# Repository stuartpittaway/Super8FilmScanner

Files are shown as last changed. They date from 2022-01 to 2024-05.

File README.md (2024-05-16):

# 3D printed Super 8 Film Scanner

Using OpenCV and Open Source software to scan and create videos from Super 8 film reel, along with a 3D printed frame.

The code and scanner were created quickly to achieve the job of scanning a handful of Super 8 reels at an acceptable quality.

The code is not optimised or user friendly, but pull requests are very welcome!

The code is unlikely to run straight out of the box on your computer/system, it will need minor amendments to folder names/paths etc.

Items needed for this project:
* [Raspberry Pi 4](https://www.raspberrypi.com/products/raspberry-pi-4-model-b/)
* [Pi Advanced 12megapixel Camera](https://www.raspberrypi.com/products/raspberry-pi-high-quality-camera/)
* [Microscope lens for the Raspberry Pi High Quality Camera - 0.12-1.8x](https://shop.pimoroni.com/products/microscope-lens-0-12-1-8x)
* 3D printed frame (files in this repository)
* Two small depth stepper motors (NEMA 17 style)
* RAMPS style motherboard for controlling the stepper motors and running [MARLIN](https://github.com/MarlinFirmware/Marlin)
* Two stepper drivers (for example A4988)
* ~5000K "cool white" MR16 style LED light bulb (5 Watt)
* 240V Power supply (an old Ender3 PSU will do)
* MicroSD card

# YouTube video

See the video on how to use and build this device.

https://youtu.be/rd1Xu6e6nrw

# Setup

This is a rough setup description and some steps might be missing, but here is what's necessary:

## Step 1 - Flash Marlin to the mainboard
Flash your mainboard with the Marlin Firmware. You can find the latest release [here](https://marlinfw.org/meta/download/).

Open Arduino IDE, make the required changes (for your mainboard), connect the Mainboard via USB and upload the firmware to the Mainboard.

## Step 2 - Install RaspOS on the Raspberry Pi
Install the Raspberry Pi Imager, which you can find [here](https://www.raspberrypi.com/software/).

Plug in the microSD card into your computer and choose to install the **Legacy 32-bit OS** in the imager software. Use CTRL+SHIFT+X to open the advanced settings.  Choose a hostname, for example "scanner". Then add a username and password. Activate SSH under "services" and add your Wifi settings.

## Step 3 - Wiring
Assemble the scanner according to the 3D files.

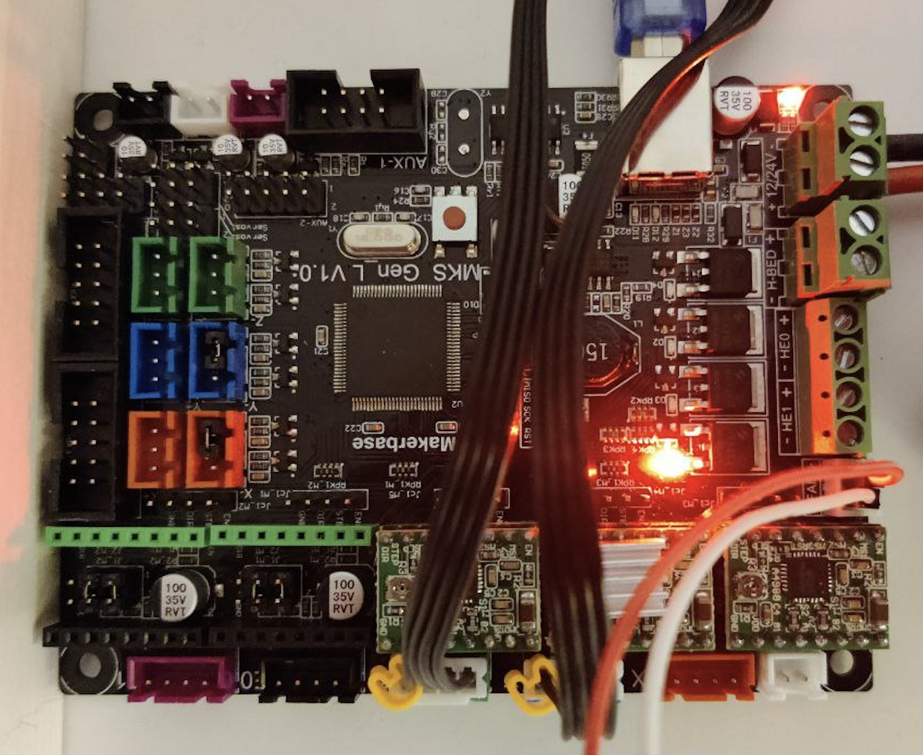
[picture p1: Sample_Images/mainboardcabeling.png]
Mainboard


Plug in the stepper drivers into the mainboards Y and Z axis, then plug in the stepper motors in these axis. You should add the heatsink to the Y axis stepper driver, as it's the one used the most.

Slot the Raspberry Pi HQ cameras ribbon cable into the Raspberry Pi and lock it in place. 

Plug the LED wires into the fan header. 

Connect the power supply to the mainboard via the two cables. Make sure the power supply is disconnected.

Connect the mainboard to the Raspberry Pi.

## Step 4 - Connecting to the Raspberry Pi
If you don't plan to use the scanner with dedicated monitor, keyboard and mouse, you have to connect to it via Terminal and VNC. 

Turn on the Raspberry Pi and the PSU. 

Use SSH to connect to <username>@scanner.local, then install VNC server to control your scanner in the future. If your screen stays black after connecting, run "vncserver-virtual" to add a virtual display. 

## Step 5 - Install dependencies
To install OpenCV, run `sudo apt-get update` , then `sudo apt-get install build-essential cmake pkg-config libjpeg-dev libtiff5-dev libjasper-dev libpng-dev libavcodec-dev libavformat-dev libswscale-dev libv4l-dev libxvidcore-dev libx264-dev libfontconfig1-dev libcairo2-dev libgdk-pixbuf2.0-dev libpango1.0-dev libgtk2.0-dev libgtk-3-dev libatlas-base-dev gfortran libhdf5-dev libhdf5-serial-dev libhdf5-103 python3-pyqt5 python3-dev -y`

you might also need to run `pip install opencv-python==4.5.3.56` .

# Scanning Process

## Step 1 - Capture full frame masters

On a Raspberry Pi (4 is possible), use the python code in `RasPi_Camera_Super8Scanner.py` to capture all the individual frames to individual PNG files.

This will generate a large number of files (3000+) of significant file size 2+MByte each.  Camera captures approximately 3megapixel images.

Scanning is slow, running around 1.25 frames per second, so a 3 minute reel takes 1 hour.  

Speed was not a critical issue when designing this solution, however the longest delay is capturing the image from the Raspberry Pi camera.

The images captured would look like this (only higher resolution).  Notice you can see the sproket hole and the black border on the right of the image.
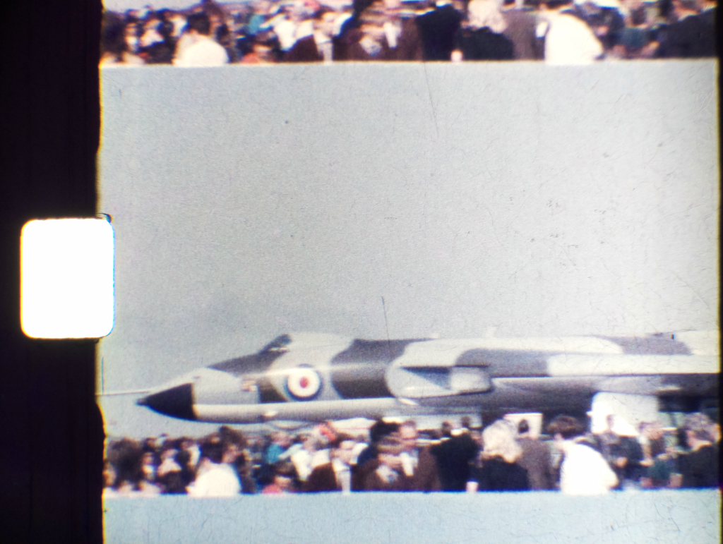
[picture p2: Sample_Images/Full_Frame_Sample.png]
Full frame sample image


## Step 2 - Alignment

Step one captured the full frame of the film, this process takes those master images and accurately crops them to vertically and horizontally align them based on the sproket hole.

OpenCV is used to detect the hole and align/crop the image.

The code is in `ImageRegistrationCropping.py` its likely you will need to tweak the code to cater for the particular file size/resolution you are using and the camera configuration.

Look for the variable `frame_dims` to control the output image dimensions.  Its likely you will also need to change the folder names.

The files are put into a folder named "Aligned".  Example image.
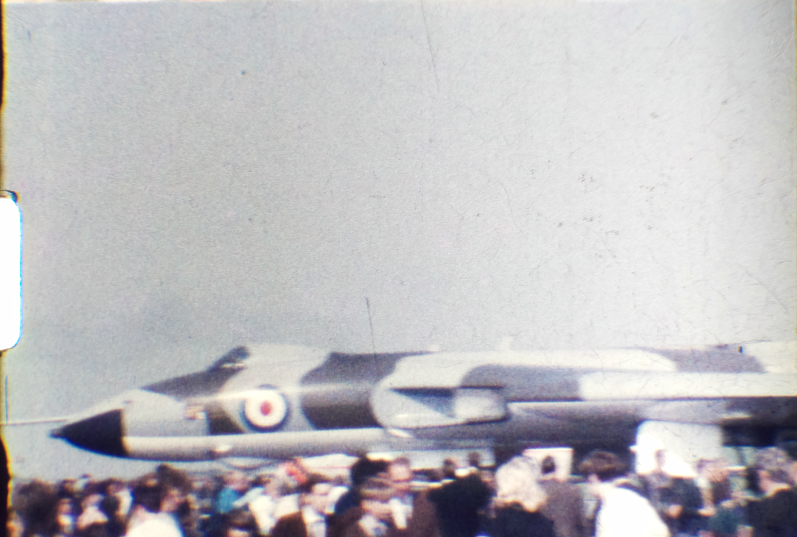
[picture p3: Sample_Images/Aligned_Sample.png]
Aligned frame sample image


You can modify the provided `config.json` file to suit your needs. These are the available configurations:

```json
{
    "image_name": "frame_????????", // The name of the images to be processed
    "input_path": "Capture", // The folder where the images are stored
    "output_path": "Aligned", // The folder where the aligned images will be stored
    "extensions": ["png", "jpg", "jpeg"], // The extensions of the images to be processed
    "average_sample_count": 11, // This will be saved automatically if you run a new analysis
    "average_width": 512, // This will be saved automatically if you run a new analysis
    "average_height": 649, // This will be saved automatically if you run a new analysis
    "average_area": 306419, // This will be saved automatically if you run a new analysis
    "resize_image": [ // if you want to resize the images after alignment
        3840, // width
        2160 // height
    ],
    "frame_dims": [ // You can get this after adjusting the first frame dimensions
        0, // x offset
        -904, // y offset
        3192, // width
        2305 // height
    ]
}
```

## Step 3 - Denoise (optional)

A post process called de-noise filtering can be used to improve image quality.  This code can be found in `Denoise.py`

This is a significantly slow process, so a faster CPU helps a lot.  You can tweak the amount of correction made with these values

```
h=3, hColor=3, templateWindowSize=7,searchWindowSize=29
```

For a description of the paramters, check out the [OpenCV documentation](https://docs.opencv.org/3.4/d1/d79/group__photo__denoise.html#gaa501e71f52fb2dc17ff8ca5e7d2d3619).

The files are put into a folder named "Denoise".  Example image.
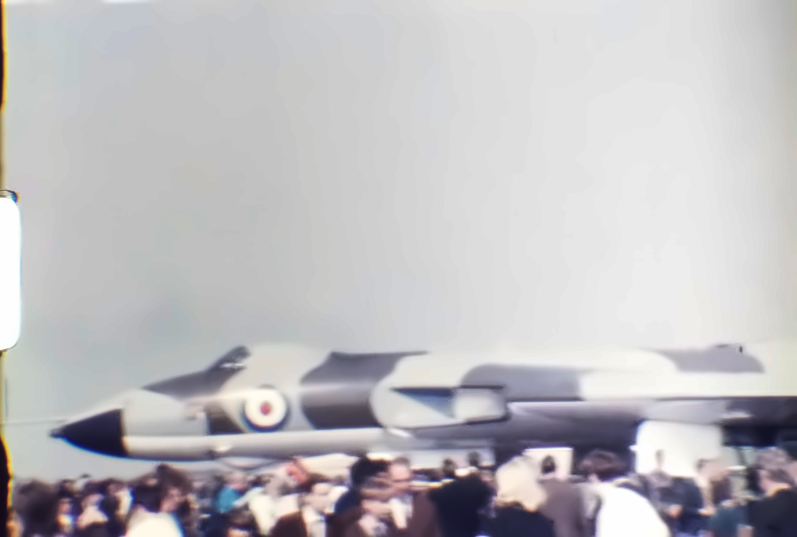
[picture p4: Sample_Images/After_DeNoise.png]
Frame after denoise filtering


## Step 4 - Create Video

### FFMPEG
You can use the open source FFMPEG tool to convert a series of pictures into a video, using a command similar to this:
```
ffmpeg.exe -y -start_number 0 -framerate 18 -i "Aligned\frame_%08d.png" -vcodec h264 -preset slower -tune grain -crf 15 -vf "fps=18,format=yuv420p" -r 18 film_output.mp4
```

### Video editor software
Alternatively, use video editing software like [Davinci Resolve](https://www.blackmagicdesign.com/products/davinciresolve/) to import the pictures and generate a video.

This can also be used to colour correct the film, remove noise and grain and generally improve the final video.

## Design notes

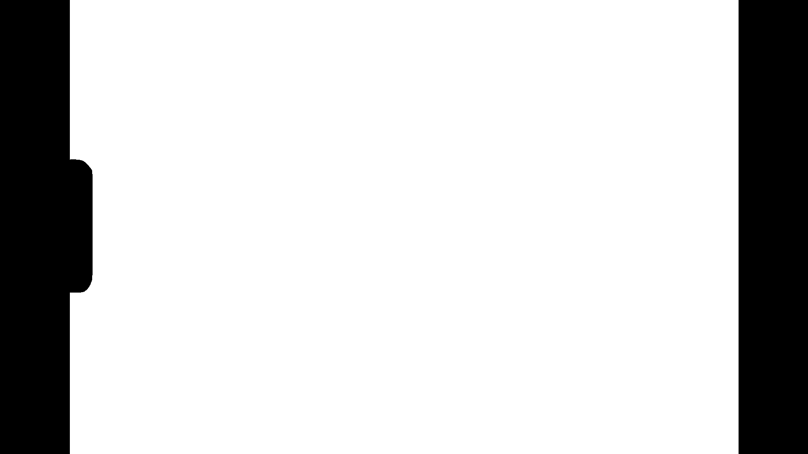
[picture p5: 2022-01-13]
Python/overlay_frame.png

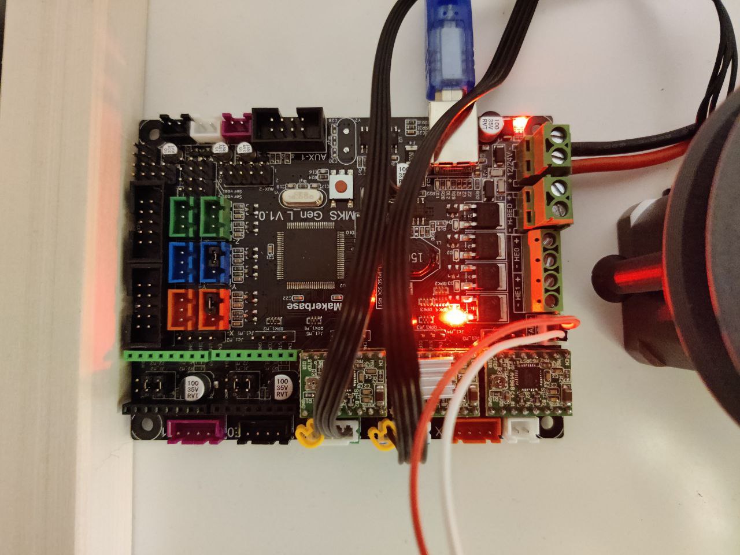
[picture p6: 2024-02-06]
Sample_Images/mainboard.jpg

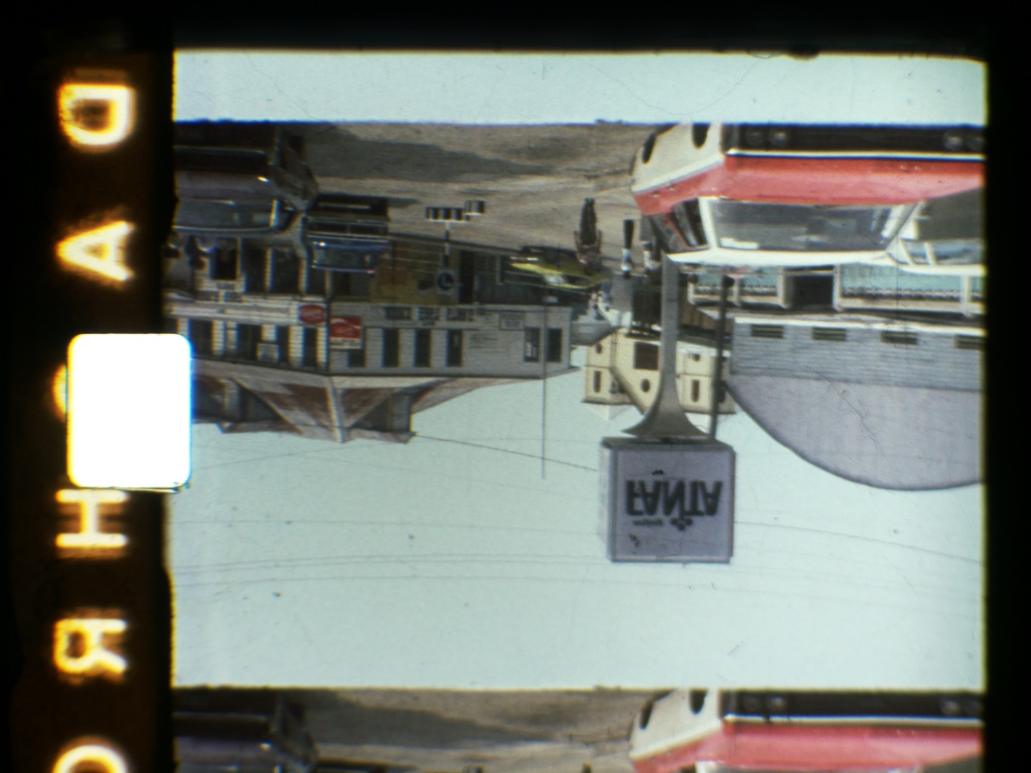
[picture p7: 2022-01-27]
Python/grab.jpg

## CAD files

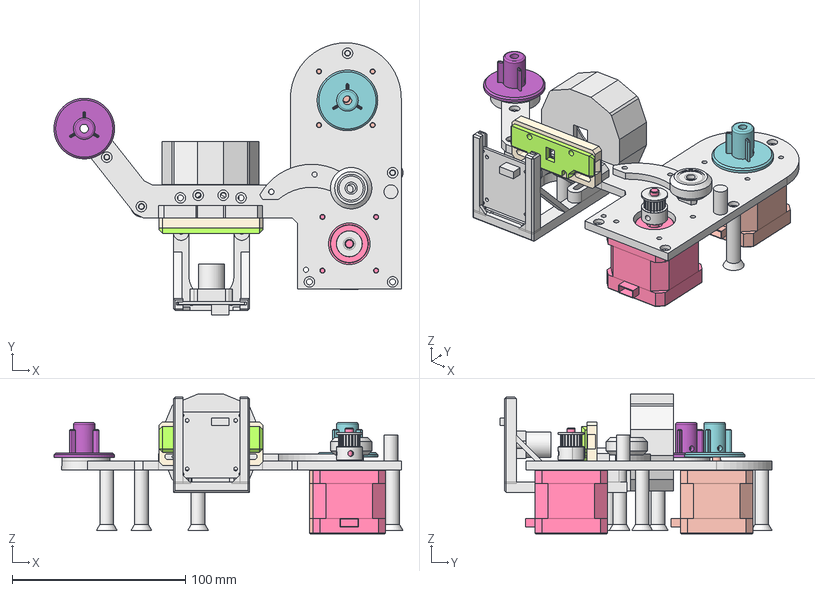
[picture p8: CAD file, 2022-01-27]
Assemby.FCStd
201.5 x 157.2 x 80.6 mm
BackPlate_Body-Arm_001
BackPlate_Body-CameraMount_001
BackPlate_Body-Frame_001
BackPlate_Body-Turret_001
BackPlate_Body-Turret_002
BackPlate_Body-Turret_003
Super8FilmScanner_Body-Gate-Back_001
Super8FilmScanner_Body-Gate-Front_001
Super8FilmScanner_Body-TapeWheel_001
Super8FilmScanner_Body-TapeWheel_002
BackPlate_Body-Turret_004
BackPlate_Body-Turret_007
BackPlate_Body-LampMount_001
OTS-0002-00_usb-webcam_Body_001
OTS-0017_GT2-20-tooth-pulley1_Gates_2GT_20T_Toothed_Pulley_001
OTS-0012_nema17-stepper1_Nema 17 42A02C v2_001
OTS-0012_nema17-stepper1_Nema 17 42A02C v2_002
OTS-0011_v-slot-roller1_Fusion_001

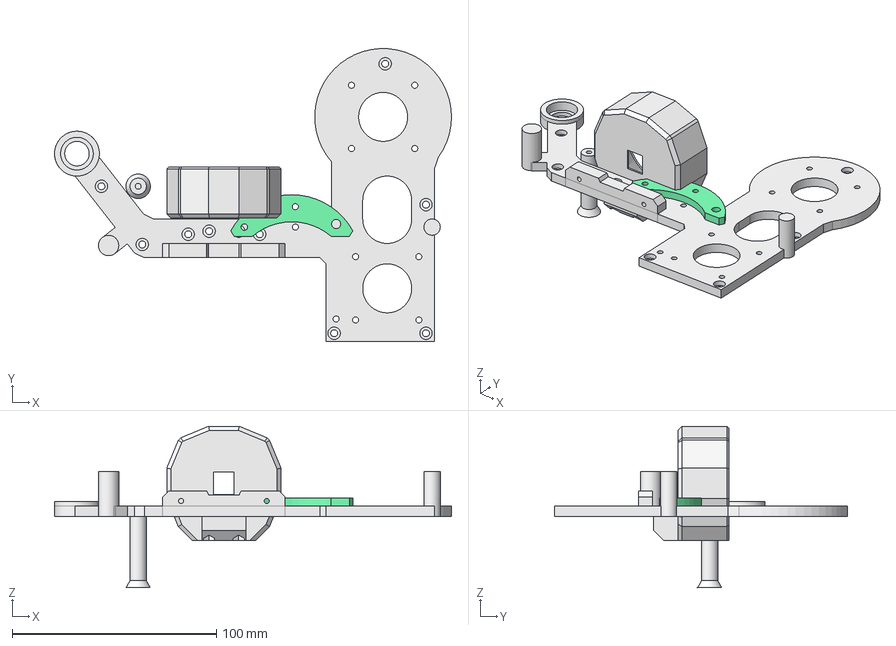
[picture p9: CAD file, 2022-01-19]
BackPlate.FCStd
194.5 x 143.5 x 79.1 mm
Body-Frame
Body-Arm
Body-Turret
Body-LampMount

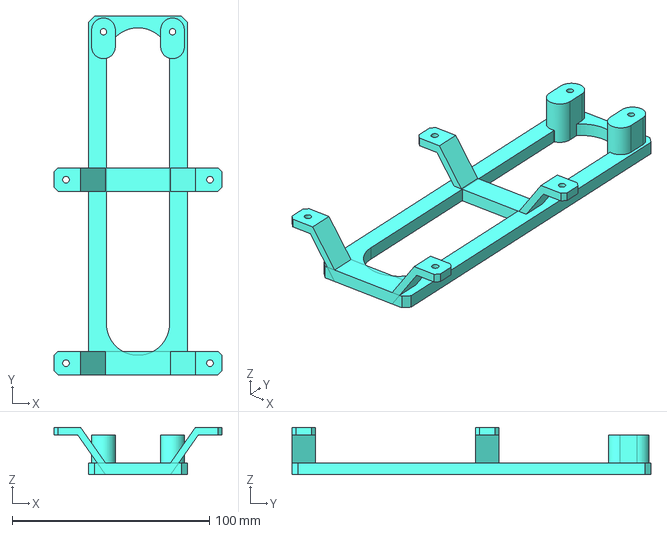
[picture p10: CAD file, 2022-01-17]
CameraMount-RaspPiAdvanced.FCStd
85.0 x 182.0 x 24.0 mm

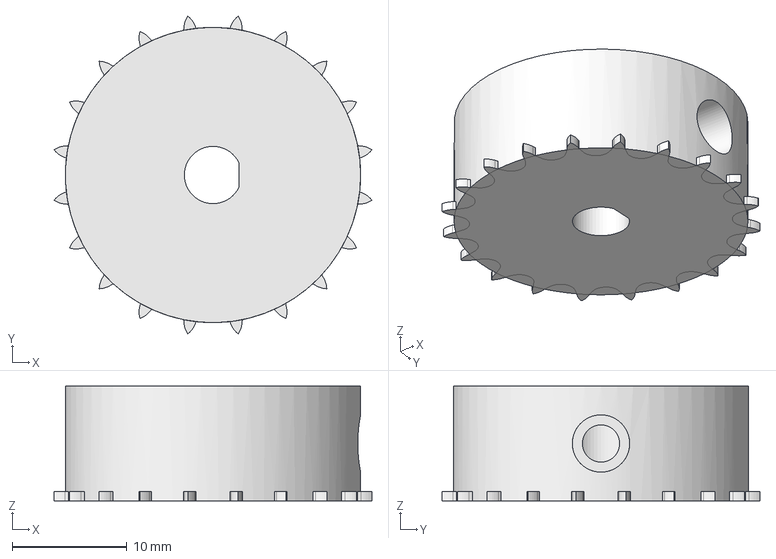
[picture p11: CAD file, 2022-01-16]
film_sproket.FCStd
27.7 x 27.7 x 10.0 mm

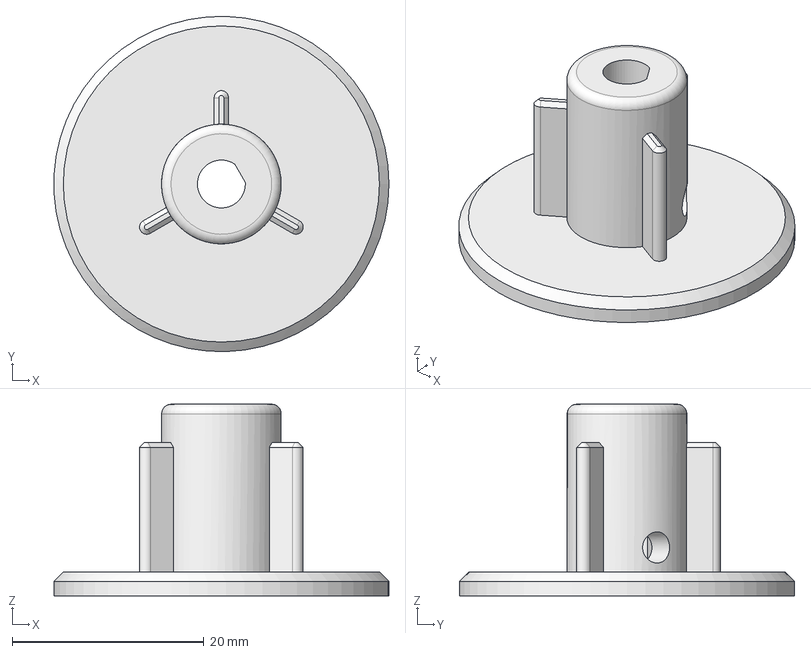
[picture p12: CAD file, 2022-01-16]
Super8FilmScanner.FCStd
35.0 x 35.0 x 20.0 mm

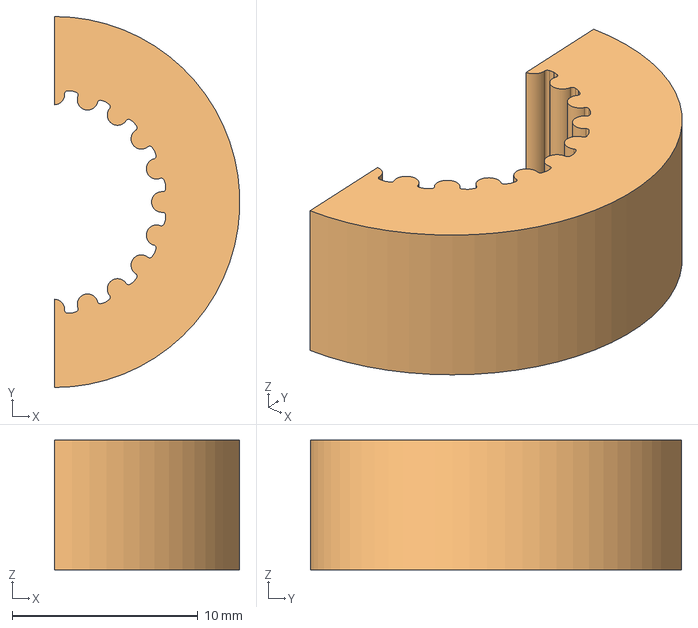
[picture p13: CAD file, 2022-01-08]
RubberWheel.FCStd
9.99 x 20.0 x 7.00 mm
Reference001(Boolean)

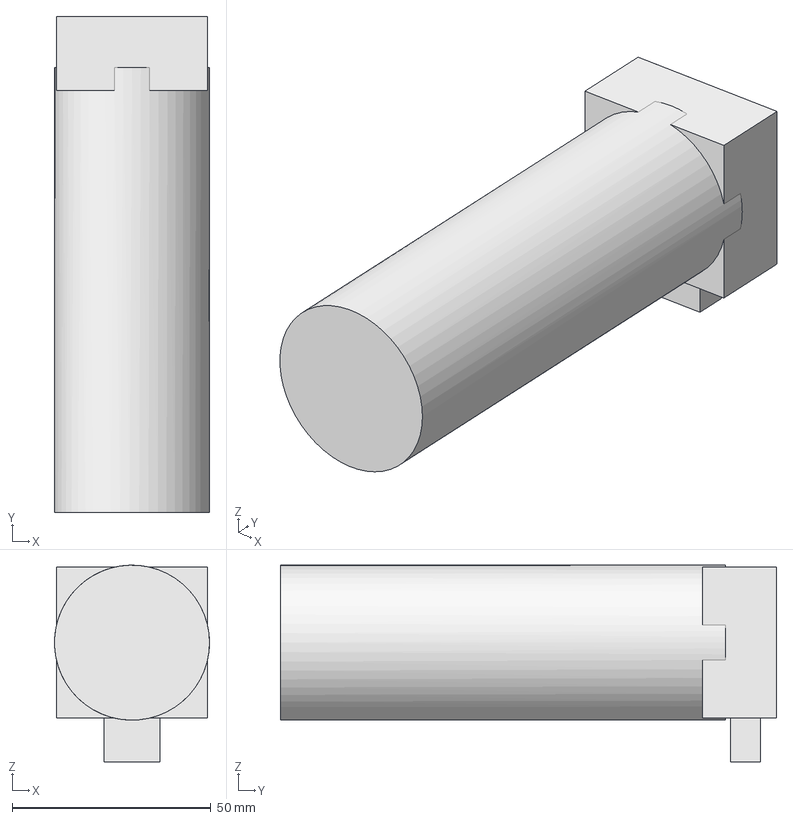
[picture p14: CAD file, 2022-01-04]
PIHQMicroscopeCamera.FCStd
39.0 x 124.8 x 49.5 mm

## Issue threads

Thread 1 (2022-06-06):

HDR bracketing

patriot1889, 2022-06-06:
Hey Stuart,

I'm just in the process of printing the parts you've designed for the structure of the scanner.

I was wondering if you had any ideas on how you could integrate bracketing to enable creating a Mertens merge image?
There is a project called YART (https://github.com/dgalland/yart), which you're probably aware of, that does this and it looks like it works very well for bringing back some shadows and highlights from the scans.

Cheers!

stuartpittaway, 2022-06-07:
I have seen that project.  I'm afraid that the details are a bit out of my depth.

I spent ages trying to improve quality, but in the end I realized that my original source material was nothing special, so just tried to make the best of what I had.

patriot1889, 2022-06-07:
No worries, thanks for the response.

I can see in the code that you have an array
`CAMERA_EXPOSURE = [-8.0,-4.0,-10.0]`

Is this remnants of toying with the idea of capturing multiple exposures?
I can do the merge elsewhere, I just need to try and figure out how to capture 3-5 exposures.

stuartpittaway, 2022-06-07:
Yes that right I did play around with multiple exposures, but the time taken to capture all the frames and merge together.

thejokoono, 2024-01-20:
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

Did you end up integrating it?

stuartpittaway, 2024-01-22:
Yes, that was me playing around - I gave up with that in the end as I wasn't trying to get the best possible picture, just something suitable to share with friends and family.

thejokoono, 2024-01-30:
I've built the printer and amazingly it works! I've scanned the first films and want to say thank you so much for providing all this info! I accidentally bought a "warm white" LED, which gives the images a red hue, so maybe it makes sense to add "cool white LED" to the list in the README.

If I set CAMERA_EXPOSURE = [-8.0,-4.0,-10.0] , it sucessfully takes 3 images, but they all have the same exposure, even with the values set very high. Anything i'm missing, or is that as far as you've implemented it?

stuartpittaway, 2024-01-31:
Well done @thejokoono great work!

You might be able to fix the warm white LED in software - automatic white balance?

I didn't get the EXPOSURE stuff to work - not sure what I was doing wrong, I suspect I'm not setting the camera parameters correctly.

I'd love to see some photos of your project - upload one here!

thejokoono, 2024-02-05:
> I'd love to see some photos of your project - upload one here!

Here's a picture of my setup. There's a lot of small changes I've made, which I might add PRs for in the coming days (like support for regular 8mm film). Instead of the microscope lens I used a 50mm 1.8 with an EF to C-mount adapter and an extension tube, which worked out great after modeling a (more or less) fitting bracket.

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

I learned a lot while building this! Thank you for the your great comments in the code.

stuartpittaway, 2024-02-06:
Thats fantastic - do you have lots of film to convert?

thejokoono, 2024-02-06:
I have roughly 50-100 reels to convert, a mix of Super8 and regular 8mm film. Some of the 8mm film is so old (60+ years) that it has gotten a very red hue. We've had someone record some of the film off a projected wall over a decade ago, but the difference between that footage and the direct scans is night and day. No interlacing, more details and a lot more dynamic range.

The biggest annoyance for me was setting the focus correctly, as the depth of field for the lens is very shallow, even at F8, and the preview image is low res. I looked for a 3d printable micro adjustment slider, but couldn't find anything. Also I don't think the pickup reel calculation works correctly for my reels and films unfortunately, but I will take a look at it again.

The biggest issue I've painfully had to find is that if you restart the scanning process, it will overwrite images stored in the output folder. To fix this, I included the date in the filename.

I adjusted the min and max sprocket size for OpenCV to identify the sprocket more reliably. So now, once I start the scanning process, it works more or less flawlessly and I hardly have to adjust anything.

stuartpittaway, 2024-02-06:
Fantastic - feel free to submit any code changes, and if you publish any of the video captures on YouTube or similar, send me a link.

stuartpittaway, 2025-08-27:
Most of the screws should be M3 sized

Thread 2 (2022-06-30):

CAD Files Missing?

janoschsimon, 2022-06-30:
Hey Stuart!
 i have download the Cad files and assembley and opende it in Freecad and it seems that the Microscope lens and sled design you show in the video are not in the cad files? i also found in the files a "film_sproket" that i didnt see in the assembly? do you have perhabs a "final" assembly that you can upload? :)
cheers and thx Janosch

stuartpittaway, 2022-07-01:
You can ignore the "film_sproket" it was an attempt at a 3d printed roller wheel/film gear - didn't work, and I used rubber wheels in the end as in the video.

All the files are in GITHUB that I have, however they also have some of the previous "didn't work" versions in it!!

If you open up the Assembly file in FreeCad - there are some parts which are not-visible, if you make these visible, you should start to see the same design I used on YouTube video.

CameraMount-RaspPiAdvanced.FCStd has multiple "body" parts in it, for the camera mount.

janoschsimon, 2022-07-01:
ARGGGGGGGGGG stupid me hahahah i didnt see the "invisible" parts hehhe now i can print everything thx a ton! :) take care Janosch

Closed 2022-07-01.

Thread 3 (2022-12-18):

Missing Marlin configuration

uepsie, 2022-12-18:
Hi Stuart
Great project!
How's MARLIN configured for running this?

stuartpittaway, 2022-12-18:
That's just a very vanilla marlin install on a no-name old 3d printer board I had.

All marlin is doing is controlling a single stepper motor, so if there's another device you have which is similar that could be used instead

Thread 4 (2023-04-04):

Microscope & Camera Sled CAD Files

wmshook, 2023-04-04:
Great project! I've printed the 3D pieces and started assembling the scanner, however having trouble getting the camera assembly to mount and align properly. Could you please post the CAD files for the sled you created for the new camera and microscope lens. Also the clamps that are on the top. I'm building a version to accommodate 7" & 9" reels, and to scan both Super 8 & Reg 8mm film. I've located some old slot car foam tires to use for the pinch rollers. Once again Brilliant project!

stuartpittaway, 2023-04-05:
Hi, all the files I used should be on GitHub, I don't have anything else!

uepsie, 2023-04-05:
Hi wmshook

>  Could you please post the CAD files for the sled you created for the new camera and microscope lens.

It's in https://github.com/stuartpittaway/Super8FilmScanner/blob/main/CameraMount-RaspPiAdvanced.FCStd you have to unhide them

wmshook, 2023-04-05:
Stuart & uepsie
Found them!! Sweet! All I have to do is print them. Thanks heaps.

Closed 2023-04-05.

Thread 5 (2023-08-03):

Camera CAD Files

dstein425, 2023-08-03:
Hello Stuart,

Great project. I am working to convert your 8mm project to 16mm to capture old 16mm football films.  I noticed the CAD files from your final design do not appear in the git hub project, particularly the parts for the camera lens to focus the view, updated sled, and brackets to lock the camera in place.  Is it please possible to post them here on github?  Cheers!

Regards - Dave

EuropaSteve, 2023-08-03:
You have to unhide the objects in FreeCad.

dstein425, 2023-08-03:
Thank you @EuropaSteve that did it.  Cheers!

Closed 2023-08-03.

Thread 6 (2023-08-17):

Scanning of 8mm movies instead of Super 8

HerrLehmannHH, 2023-08-17:
Hi Stuart,

I came across your cool project on youtube. I have rebuilded everything, but at the end I figured out, that my inherited film rolls are 8mm instead of Super 8. Almost everything ist the same except the sprocket holes, they are not centered with each frame, but they are in between.

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

Is there a chance to adapt this behaviour? What variables are relevant?

Kind regards,
Dirk

PS.:
sorry writing an issue as an email

stuartpittaway, 2023-08-17:
Hello, thank you for the interest in this project.

The sproket should be easy to change in FreeCAD - its created using the gear feature so should be editable for the gear/tooth distance you need.

stuartpittaway, 2023-08-17:
Ah ok.

In the Python code file RasPi_Camera_Super8Scanner.py look at link 653...

```
        # Default space (in marlin Y units) between frames on the reel
        FRAME_SPACING = 16.42
```

Increase the 16.42 number until you find something suitable for your film reel size.

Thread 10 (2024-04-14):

HQ Camera Microscope Lens Mount Bracket missing

j-pickens, 2024-04-14:
I have looked through all the assembly files, and cannot find the HQ camera/microscope lens mounting brackets.
The FSCAD assembly files only show a generic tube shape for the lens, and the tapered mount shown in the Youtube video is no where to be found.  At least by my inexperienced Freecad usage.

Here are the files I examined:
CameraMount-RaspPiAdvanced.FCStd
PIHQMicroscopeCamera.FCStd
Super8FilmScanner.FCStd
Assemby.FCStd

Am I missing something?
Thanks for this project.  I plan to put this together and modify it for full size Super8mm film reels

stuartpittaway, 2024-04-15:
Ok - I suspect the models are hidden (from display) in the freecad files.  See if any of the models in FreeCad show as greyed out - if so click the eye symbol next to them to enable/show.

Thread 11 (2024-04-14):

Raspberry Pi OS have moved from libmmal.so to use libcamera

OneGherkinTwoOlives, 2024-04-14:
I came across you project and have been working on building it out for .... a while.  I have all the pieces together but am running into issues with what I understand to the best of my limited knowledge, is the Raspberry OS has changed some of the dependencies.  I'm not sure if there are others, but from what I have read, Pi no longer uses libmmal.so.

I haven't been able to install it when running the current OS (12 bookworm).  Honestly, this is my first foray into modifying any code. I've started to learn some Python basics, but I modifying to change how the the script works might be a bit out of my depth.

I just wanted to see if anyone had updated the script to work with the most recent libcamera, or if there was another work around.

stuartpittaway, 2024-04-15:
I only built this project as a "one off" to transfer some old film so I've not kept up to date with changes in the PI OS or the Python libraries so will need to be changed to keep up with modern versions

gpayant, 2024-04-22:
Hello,
As I'm not a coder, I'd also be interested in having an update for the latest versions of OpenCV and Raspberry OS.
I have a Raspberry P5 to do this project and I'm not sure I have the skills to make the code changes myself :-( .
Thanks

ge0ff042, 2024-06-04:
I'm also on Rpi5 (Bookworm 64bit). From what I can see picamera was replaced by picamera2. https://github.com/raspberrypi/picamera2. I'll be attempting to make the orig code and the new code that thejokoono submitted for standard 8mm work on bookworm and I will share when I'm done.

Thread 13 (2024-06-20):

Could this theoretically be modified to scan 35mm film?

shealan, 2024-06-20:
I have some 35mm film trailers I would love to transfer.

stuartpittaway, 2024-06-22:
Yes, no reason why not, just a wider/larger 3d printed part.

Closed 2024-06-22.

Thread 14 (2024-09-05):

SyntaxError: Invalid syntax

elgato45, 2024-09-05:
Hi Stuart, thanks for your project. I'm trying to run your code but I'm getting this error, I have python version 2.7.18.

python RasPi_Camera_Super8Scanner.py
  File "RasPi_Camera_Super8Scanner.py", line 62
    def MarlinWaitForReply(MarlinSerialPort: serial.Serial, echoToPrint=True) bool:
                                           ^
SyntaxError: invalid syntax

stuartpittaway, 2024-09-05:
Python 2.7 is quite old now, can you try V3?

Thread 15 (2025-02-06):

Adapt for 9.5mm film ?

nicholgd, 2025-02-06:
First of all thanks for publishing the details of your work.
As the title says .I have a number of 9.5mm film that needs to be scanned.
9.5mm film has the sprocket hole in the centre of the film between each frame.
Would it be fairly easy to adapt your python script ?
Any pointers would be very welcome.
the hardware is being printed with adaptions for 9.5mm film. MKS gen L programmed and working.
jus need to mod the script.

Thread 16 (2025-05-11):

Large reels?

robustini, 2025-05-11:
Thank you for the great project!
I didn't quite understand from the documentation how it handles the two NEMA17s, i.e., how it makes the film always stay tightly wound on the output coil.
I understand that every single frame is detected by an algorithm that intercepts the drag hole, right?
Other than that, I have several 20cm reels, wasn't a larger frame designed?
Regards,
Marco

stuartpittaway, 2025-05-11:
The code keeps track of how much film has been used and tightens up the slack in the reels.

You could fit larger reels, would just need the arms lengthening

robustini, 2025-05-12:
Also I see from your movie that there is a particular molded stand to attach the 100x microscope but I don't see this printable support in your project.

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

stuartpittaway, 2025-05-12:
Yes the repo is correct. I believe some of the parts are toggled off/not visible in freecad - just need the visibility toggling back on.

I've not touched this project for a few years now, and don't have the time to amend the machine for a larger size.

You may be able to take the 3d parts into fusion 360 and stretch them?

robustini, 2025-05-12:
Work in progress...

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

robustini, 2025-05-12:
@stuartpittaway please check because the support for the 100x microscope that you see in the video does not exist in the project you posted, or at least I don't see it in FreeCAD.

robustini, 2025-05-12:
> The code keeps track of how much film has been used and tightens up the slack in the reels.

If you use the molded reel from the project maybe yes, but with another one that maybe has a different internal diameter I don't think it would work well, right?

burgsth, 2025-05-13:
Could you please share your 20cm reel version?  Maybe there is also an additional deflection needed ob the input side caused by the significant different angle if the spool is getting to its end.

robustini, 2025-05-13:
> Could you please share your 20cm reel version? Maybe there is also an additional deflection needed ob the input side caused by the significant different angle if the spool is getting to its end.

I had already corrected it but thanks for bringing it to my attention.
I don't know if I will continue with this project, I don't really like that the reel that retrieves the film doesn't have a control of when to activate and stop.

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

stuartpittaway, 2025-05-13:
> [@stuartpittaway](https://github.com/stuartpittaway) please check because the support for the 100x microscope that you see in the video does not exist in the project you posted, or at least I don't see it in FreeCAD.

Look in the file CameraMount-RaspPiAdvanced.FCStd for the Rasp PI advanced camera parts.

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

stuartpittaway, 2025-05-13:
> I don't know if I will continue with this project, I don't really like that the reel that retrieves the film doesn't have a control of when to activate and stop, such as with T-Scann 8 is expected.

I didn't find it a problem on the dozen or so reels I scanned - although they were all the smaller reel sizes.

The lower motor pulls the film through, the source film is simply free spinning.

Once the code has determined there is some slack in the film, the take up reel is rotated to pick up the slack - not perfect, but worked okay for what I wanted to do.

You can obviously sit and watch the whole process and manually turn the pick up reel if you wish instead.

robustini, 2025-05-13:
> Once the code has determined there is some slack in the film, the take up reel is rotated to pick up the slack - not perfect, but worked okay for what I wanted to do.
>
> You can obviously sit and watch the whole process and manually turn the pick up reel if you wish instead.

Certainly with small reels it can work, but with large reels in my opinion a huge error will be generated.
It is unthinkable to stand in front of the scanner for many hours to retrieve the film manually.
The 3d printer board has many connectors for mechanical or optical endstops, it would be useful to implement something that activates the stepper of that reel only when really needed.

stuartpittaway, 2025-05-13:
Agreed, plenty of inputs on the 3d board for some sort of sensor.

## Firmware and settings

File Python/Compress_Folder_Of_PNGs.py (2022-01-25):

# Compress_Folder_Of_PNGs.py
# Simple script to copy images from one folder to another
# converting/compressing PNG along the way
# to aid in reducing disk space and reducing CPU load on Rasp PI
import numpy as np
import cv2 as cv
import time
import glob
import os

def Filelist(path: str, ext: str) -> int:
    return sorted(glob.glob(os.path.join(path, "frame_????????."+ext)), reverse=True)

output_path = os.path.join(os.getcwd(), "Capture")
if not os.path.exists(output_path):
    raise FileNotFoundError("Missing output folder")

input_path = "\\\\192.168.0.66\\pi\\Super8FilmScanner\\Python\\Capture-8.0"
if not os.path.exists(input_path):
    raise FileNotFoundError("Missing input folder")

while True:
    # Scan for bitmap files to convert, skip first one (most recent) in cas its being written to
    files=Filelist(input_path,"bmp")
    if len(files)==0:
        print("Nothing to do, so quit...")
        quit()

    for filename in files[2:]:
        img = cv.imread(filename,cv.IMREAD_UNCHANGED)
        if img is None:
            print("Error opening file",filename)
        else:
            output_filename=os.path.join(output_path,os.path.splitext(os.path.basename(filename))[0]+'.png')
        
            start_time=time.perf_counter()
            # PNG output, with NO compression - which is quicker (less CPU time) on Rasp PI
            # at expense of disk I/O. PNG is always lossless
            if cv.imwrite(output_filename, img, [cv.IMWRITE_PNG_COMPRESSION, 3])==True:
                print("Save image took {:.2f} seconds".format(time.perf_counter() - start_time))
                #Delete source file
                os.remove(filename)
                print("Deleted",filename)
            else:
                raise IOError("Failed to save image")

    time.sleep(20)

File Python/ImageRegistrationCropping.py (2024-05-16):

from __future__ import annotations
from typing import TYPE_CHECKING, List
from threading import Thread

import cv2 as cv
import numpy as np
import os
import glob
import shutil
import traceback
import json
import queue

NUM_THREADS = 2

q = queue.Queue(maxsize=10)

min_x=999999
max_x=0
min_y=999999
max_y=0
lower_t=225
previous_frame_top_left_of_sproket_hole=None
previous_frame_bottom_right_of_sproket_hole=None
frame_dims=(0,0, 800, 540)

def ServiceImageWriteQueue(q):
    while True:
        data=q.get(block=True, timeout=None)

        if cv.imwrite(data["filename"], data["image"], [cv.IMWRITE_PNG_COMPRESSION,1])==False:
            raise IOError("Failed to save image")

        q.task_done()

def OutputFolder(path: str) -> str:
    # Create folders for the different EV exposure levels
    
    # Image Output path - create if needed
    path = os.path.join(os.getcwd(), path)

    if not os.path.exists(path):
        os.mkdir(path)

    return path

def ImageFolder(path: str) -> str:  
    # Image Input path - create if needed
    path = os.path.join(os.getcwd(), path)

    if not os.path.exists(path):
        raise FileNotFoundError(path)

    return path

def Filelist(path: str, extensions: list, name:str) -> list:
    """ Generate a list of files from given path with specified extensions, sorted by filename. """
    files = []
    for ext in extensions:
        files.extend(glob.glob(os.path.join(path, f"{name}.{ext}")))
    files = sorted(files)  # Sort the files after collecting all extensions
    return files

# For Details Reference Link:
# http://stackoverflow.com/questions/46036477/drawing-fancy-rectangle-around-face
def draw_border(img, pt1, pt2, color, thickness, r, d):
    x1,y1 = pt1
    x2,y2 = pt2

    # Top left
    cv.line(img, (x1 + r, y1), (x1 + r + d, y1), color, thickness)
    cv.line(img, (x1, y1 + r), (x1, y1 + r + d), color, thickness)
    cv.ellipse(img, (x1 + r, y1 + r), (r, r), 180, 0, 90, color, thickness)

    # Top right
    cv.line(img, (x2 - r, y1), (x2 - r - d, y1), color, thickness)
    cv.line(img, (x2, y1 + r), (x2, y1 + r + d), color, thickness)
    cv.ellipse(img, (x2 - r, y1 + r), (r, r), 270, 0, 90, color, thickness)

    # Bottom left
    cv.line(img, (x1 + r, y2), (x1 + r + d, y2), color, thickness)
    cv.line(img, (x1, y2 - r), (x1, y2 - r - d), color, thickness)
    cv.ellipse(img, (x1 + r, y2 - r), (r, r), 90, 0, 90, color, thickness)

    # Bottom right
    cv.line(img, (x2 - r, y2), (x2 - r - d, y2), color, thickness)
    cv.line(img, (x2, y2 - r), (x2, y2 - r - d), color, thickness)
    cv.ellipse(img, (x2 - r, y2 - r), (r, r), 0, 0, 90, color, thickness)

def detectSproket(sproket_image, lower_threshold:int=210):
    # Convert to gray and blur
    matrix = (3, 7)
    sproket_image = cv.GaussianBlur(sproket_image, matrix, 0)
    
    sproket_image = cv.cvtColor(sproket_image, cv.COLOR_BGR2GRAY)

    sproket_image = cv.equalizeHist(sproket_image)
    # Threshold
    _, sproket_image = cv.threshold(sproket_image, lower_threshold, 255, cv.THRESH_BINARY)    

    cv.imshow("sproket_image",cv.resize(sproket_image, (0,0), fx=0.4, fy=0.4))

    # Detect the sproket shape
    contours, _ = cv.findContours(sproket_image, cv.RETR_EXTERNAL, cv.CHAIN_APPROX_SIMPLE)

    #cv.drawContours(image, contours, -1,color=(0,0,255), thickness=cv.FILLED)

    #Abort here if detection found nothing!
    if len(contours)==0:
        #Return a fake reading (hard coded)
        return (455, 646), (455, 646),1,1, 0, 1, len(contours)

    # Sort by area, largest first (hopefully our sproket - we should only have 1 full sprocket in view at any 1 time)
    contour = sorted(contours, key=lambda x: cv.contourArea(x), reverse=True)[0]      

    #colour = (100, 100, 100)
    #cv.drawContours(sproket_image, [contour], -1,color=colour, thickness=cv.FILLED)

    area = cv.contourArea(contour)
    rect = cv.minAreaRect(contour)
    rotation = rect[2]
    centre = rect[0]
    # Gets center of rotated rectangle
    box = cv.boxPoints(rect)
    # Convert dimensions to ints
    box = np.int0(box)

    #print("area",area)
    #print("rotation",rotation)

    a=min(box[0][0],box[1][0],box[2][0],box[3][0])
    b=min(box[0][1],box[1][1],box[2][1],box[3][1])
    top_left_of_sproket_hole=(a,b)

    a=max(box[0][0],box[1][0],box[2][0],box[3][0])
    b=max(box[0][1],box[1][1],box[2][1],box[3][1])
    bottom_right_of_sproket_hole=(a,b)
    #cv.drawContours(sproket_image, [box], -1,color=(200, 0, 0), thickness=2)

    # Check for vertical stretch
    height_of_sproket_hole=bottom_right_of_sproket_hole[1]-top_left_of_sproket_hole[1]
 
    # Check width
    width_of_sproket_hole=bottom_right_of_sproket_hole[0]-top_left_of_sproket_hole[0]

    #print(top_left_of_sproket_hole, bottom_right_of_sproket_hole)
    #cv.rectangle(sproket_image, top_left_of_sproket_hole, bottom_right_of_sproket_hole, 255, 4)
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

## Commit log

2022-01-01 Minor changes to cad models
    [Assemby.FCStd, BackPlate.FCStd, Super8FilmScanner.FCStd]
2022-01-04 CAD updates
    [Assemby.FCStd, BackPlate.FCStd, CameraMount-RaspPiAdvanced.FCStd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]
2022-01-07 Larger mount
    [Assemby.FCStd, CameraMount-RaspPiAdvanced.FCStd]
2022-01-09 Updated frame
2022-01-10 Working capture using high res camera (very slowly)
2022-01-17 Lamp mount
    [Assemby.FCStd, BackPlate.FCStd, CameraMount-RaspPiAdvanced.FCStd]
2022-01-21 Added multi-thread saving routing to boost speed of capture
2022-01-21 Multi thread saving of images
2024-05-13 allow for frame dimesions adjusts
2024-05-13 retry if not enough sprocket data
